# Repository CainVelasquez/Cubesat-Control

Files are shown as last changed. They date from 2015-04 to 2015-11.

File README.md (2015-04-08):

# Cubesat Controle

## Descrição
Desenvolvimento do sistema de controle de atitude

## Envolvidos
- Felipe
- Augusto
- William

## Organização das pastas

As pastas desse projeto devem ser organizadas conforme exemplo a seguir:

- Como : Toda documentação gerada e coletada que pode ser usada para compreenção e descrição do projeto

- Materiais : Todo formato de material desenvolvido no projeto, inclui softwares, esquemáticos, fotos, etc..

Árvore de arquivos :
```
└──  Materiais
├── Como
│   ├── Apresentações
│   ├── Artigos
│   │   └── Bibliografia
│   ├── Datasheets
│   ├── Estudos
│   ├── Manuais
│   └── Wiki
└──  Materiais
    ├── Arquivos
    │   └── Orçamentos
    ├── Códigos
    │   ├── Altera
    │   ├── Arduino
    │   ├── Atmel
    │   ├── C
    │   ├── Comsol
    │   ├── Labview
    │   ├── Matlab
    │   └── Xilinx
    ├── Fotos
    ├── Mecânica
    ├── PCB
    └── Referências
```

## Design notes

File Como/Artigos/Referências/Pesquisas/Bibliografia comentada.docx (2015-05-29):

| FLORENZANO, Teresa Gallotti. Iniciação em sensoriamento remoto. 3. ed. rev. e ampl. São Paulo, SP: Oficina de Textos, 2011. 128 p. ISBN 9788579750168.

- Utilizaremos para levantamento de histórico e informações básicas de funcionamento de satélites em geral;

| MISRA, Pratap; ENGE, Per. Global positioning system: signals, measurements, and performance. 2. ed. Massachusetts: Lincoln, 2011. 569 p. ISBN 9780970954428.

- Utilizaremos como base para posicionamento global, e informações básicas de funcionamento de satélite;

F.A.Martins_2014 - Projeto e desenvolvimento de um controlador de motores brushless para aplicação em volantes de inérica

- Utilizaremos como base este mestrado para o desenvolvimento do controle do motor BLDC. Aqui foi realizada uma placa com microcontrolador PIC, para acionamento do motor.

Brushless DC Motor Control Made Easy – AN857 Microchip

- Aqui temos um breve descritivo de como é o funcionamento de motores BLDC, e formas de controle, com sensores, ou sensorless. Open loop, closed-loop.

dsPICDEMTM MCLV DEVELOPMENT BOARD USER’S GUIDE

- Aqui é descrito o funcionamento da placa que utilizaremos para teste do motor BLDC, com exemplos de aplicação no ambiente MPLAB, e toda a parte eletrônica já realizada.

Sensored BLDC Motor Control Using dsPIC30F2010 AN957 Microchip

- Modelo de programa no MPLAB em linguagem C, para controle de motor BLDC;

Motor Maxon 351100

- Valores teóricos do motor, e especificações técnicas;

CONTROLE DE ATITUDE DE SATÉLITES ARTIFICIAIS – Trabalho de mestrado da ADRIELLE DE CARVALHO SANTANA

- Trabalho que será utilizado como guia para desenho do controle de atitude do Satelite

CubeSatBook – Princeton Satellite Systems, Inc.

- Guia de elaboração de um cubestat

CubeSat ELaNa III Launch on NPP Mission

- Exemplos de satelities lançados pela NASA

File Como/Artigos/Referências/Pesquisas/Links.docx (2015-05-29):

# Cubesat Attitude Control

https://www.youtube.com/watch?v=qoVHP34SqNg

# Reaction Wheel Pendulum

https://www.youtube.com/watch?v=UfKAn0wmxI0

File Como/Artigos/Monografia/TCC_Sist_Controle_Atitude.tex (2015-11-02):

%% abtex2-modelo-trabalho-academico.tex, v-1.9.1 laurocesar
%% Copyright 2012-2013 by abnTeX2 group at http://abntex2.googlecode.com/ 
%%
%% This work may be distributed and/or modified under the
%% conditions of the LaTeX Project Public License, either version 1.3
%% of this license or (at your option) any later version.
%% The latest version of this license is in
%%   http://www.latex-project.org/lppl.txt
%% and version 1.3 or later is part of all distributions of LaTeX
%% version 2005/12/01 or later.
%%
%% This work has the LPPL maintenance status `maintained'.
%% 
%% The Current Maintainer of this work is the abnTeX2 team, led
%% by Lauro César Araujo. Further information are available on 
%% http://abntex2.googlecode.com/
%%
%% This work consists of the files abntex2-modelo-trabalho-academico.tex,
%% abntex2-modelo-include-comandos and abntex2-modelo-references.bib
%%
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
	twoside,			% para impressão em páginas corretamente
	a4paper,			% tamanho do papel. 
	% -- opções da classe abntex2 --
	%chapter=TITLE,		% títulos de capítulos convertidos em letras maiúsculas
	%section=TITLE,		% títulos de seções convertidos em letras maiúsculas
	%subsection=TITLE,	% títulos de subseções convertidos em letras maiúsculas
	%subsubsection=TITLE,% títulos de subsubseções convertidos em letras maiúsculas
	% -- opções do pacote babel --
	english,			% idioma adicional para hifenização
	french,				% idioma adicional para hifenização
	spanish,			% idioma adicional para hifenização
	brazil,				% o último idioma é o principal do documento
	oldfontcommands
	]{abntex2}

% ---
% Pacotes básicos 
% ---
\usepackage{lmodern}			% Usa a fonte Latin Modern			
\usepackage[T1]{fontenc}		% Selecao de codigos de fonte.
\usepackage[utf8]{inputenc}		% Codificacao do documento (conversão automática dos acentos)
\usepackage{lastpage}			% Usado pela Ficha catalográfica
\usepackage{indentfirst}		% Indenta o primeiro parágrafo de cada seção.
\usepackage{color}				% Controle das cores
\usepackage{graphicx}			% Inclusão de gráficos
\usepackage{microtype} 			% Melhorias de justificação
\usepackage{pdfpages}			% Inserir páginas de pdf
\usepackage{amsmath}			% Funções Matemáticas
\usepackage{epstopdf}
% ---
		
% ---
% Pacotes adicionais, usados apenas no âmbito do Modelo Canônico do abnteX2
% ---
\usepackage{lipsum}				% para geração de dummy text
% ---

% ---
% Pacotes de citações
% ---
\usepackage[brazilian,hyperpageref]{backref}
% Paginas com as citações na bibl
\usepackage[num]{abntex2cite}	% Citações padrão ABNT

% --- 
% CONFIGURAÇÕES DE PACOTES
% --- 

% ---
% Configurações do pacote backref
% Usado sem a opção hyperpageref de backref
\renewcommand{\backrefpagesname}{Citado na(s) página(s):~}
% Texto padrão antes do número das páginas
\renewcommand{\backref}{}
% Define os textos da citação
\renewcommand*{\backrefalt}[4]{
	\ifcase #1 %
		Nenhuma citação no texto.%
	\or
		Citado na página #2.%
	\else
		Citado #1 vezes nas páginas #2.%
	\fi}%
% ---

% ---
% Informações de dados para CAPA e FOLHA DE ROSTO
% ---
\titulo{Sistema de controle de atitude para satélite CubeSat}
\autor{Augusto Bonangelo Costa\\
Felipe Ramos de Faria\\
William Mazi}
\local{São Caetano do Sul}
\data{2015}
\orientador{Prof. Dr. Rodrigo Alvite Romano}
%\coorientador{Professor}
\instituicao{Escola de Engenharia Mauá do Centro Universitário do Instituto Mauá de Tecnologia}
\tipotrabalho{Trabalho de Conclusão de Curso de Engenharia de Controle e Automação}
% O preambulo deve conter o tipo do trabalho, o objetivo, 
% o nome da instituição e a área de concentração 
\preambulo{Trabalho de Conclusão de Curso apresentado à Escola de Engenharia Mauá do Centro Universitário do Instituto Mauá de Tecnologia como requisito parcial para a obtenção do título de Engenheiro de Controle e Automação.}
% ---

% ---
% Configurações de aparência do PDF final

% alterando o aspecto da cor azul
\definecolor{blue}{RGB}{41,5,195}

% informações do PDF
\makeatletter
\hypersetup{
     	%pagebackref=true,
		pdftitle={\@title}, 
		pdfauthor={\@author},
    	pdfsubject={\imprimirpreambulo},
	    pdfcreator={LaTeX with abnTeX2},
		pdfkeywords={abnt}{latex}{abntex}{abntex2}{trabalho acadêmico}, 
		colorlinks=true,       		% false: boxed links; true: colored links
    	linkcolor=black,          	% color of internal links
    	citecolor=black,        	% color of links to bibliography
    	filecolor=black,      		% color of file links
		urlcolor=black,
		bookmarksdepth=4 
}
\makeatother
% --- 

% --- 
% Espaçamentos entre linhas e parágrafos 
% --- 

% O tamanho do parágrafo é dado por:
\setlength{\parindent}{1.25cm}

% Controle do espaçamento entre um parágrafo e outro:
\setlength{\parskip}{0.2cm}  % tente também \onelineskip

% ---
% compila o indice
% ---
\makeindex
% ---

% ----
% Início do documento
% ----
\begin{document}

% Retira espaço extra obsoleto entre as frases.
\frenchspacing

% ----------------------------------------------------------
% ELEMENTOS PRÉ-TEXTUAIS
% ----------------------------------------------------------
% \pretextual

% ---
% Capa
% ---
\imprimircapa
% ---

% ---
% Folha de rosto
% (o * indica que haverá a ficha bibliográfica)
% ---
\imprimirfolhaderosto*
% ---

% ---
% Inserir a ficha bibliografica
% ---

% Isto é um exemplo de Ficha Catalográfica, ou ``Dados internacionais de
% catalogação-na-publicação''. Você pode utilizar este modelo como referência. 
% Porém, provavelmente a biblioteca da sua universidade lhe fornecerá um PDF
% com a ficha catalográfica definitiva após a defesa do trabalho. Quando estiver
% com o documento, salve-o como PDF no diretório do seu projeto e substitua todo
% o conteúdo de implementação deste arquivo pelo comando abaixo:
%
% \begin{fichacatalografica}
%     \includepdf{fig_ficha_catalografica.pdf}
% \end{fichacatalografica}
\begin{fichacatalografica}
	\vspace*{\fill}					% Posição vertical
	\hrule							% Linha horizontal
	\begin{center}					% Minipage Centralizado
	\begin{minipage}[c]{12.5cm}		% Largura
	
	Costa, Augusto Bonangelo Costa
	
	\hspace{0.5cm} \imprimirtitulo  / Augusto Bonangelo Costa, Felipe Ramos de Faria, William Mazi. --
	\imprimirlocal, CEUN-IMT, \imprimirdata
	
	\hspace{0.5cm} \pageref{LastPage} p.\\
	
	\hspace{0.5cm}
	\parbox[t]{\textwidth}{\imprimirtipotrabalho~--~\imprimirinstituicao,
	\imprimirlocal, \imprimirdata.}\\
	
	\hspace{0.5cm} \imprimirorientadorRotulo~\imprimirorientador\\
	
	\hspace{0.5cm}
		1. Controle de Atitude.
		2. CubeSat.
		I. Faria, Felipe Ramos de
		II. Mazi, William
		III. Instituto Mauá de Tecnologia. Centro Universitário. Escola de Engenharia Mauá.
		IV. Título\\ 			
	
%	\hspace{8.75cm} CDU \\
	
	\end{minipage}
	\end{center}
	\hrule
\end{fichacatalografica}
% ---

% ---
% Inserir folha de aprovação
% ---

% Isto é um exemplo de Folha de aprovação, elemento obrigatório da NBR
% 14724/2011 (seção 4.2.1.3). Você pode utilizar este modelo até a aprovação
% do trabalho. Após isso, substitua todo o conteúdo deste arquivo por uma
% imagem da página assinada pela banca com o comando abaixo:
%
% \includepdf{folhadeaprovacao_final.pdf}
%
\begin{folhadeaprovacao}

  \begin{center}
    {\ABNTEXchapterfont\large\imprimirautor}

    \vspace*{\fill}\vspace*{\fill}
    \begin{center}
      \ABNTEXchapterfont\bfseries\Large\imprimirtitulo
    \end{center}
    \vspace*{\fill}
    
    \hspace{.45\textwidth}
    \begin{minipage}{.5\textwidth}
    \end{minipage}%
    \vspace*{\fill}
   \end{center}
        
Trabalho de Conclusão de Curso aprovado em \_\_\_ de \_\_\_\_\_\_\_\_\_\_\_\_\_ de 2015, pela banca examinadora composta por: 

   \assinatura{\textbf{\imprimirorientador} \\ Orientador} 
   \assinatura{\textbf{Professor} \\ Convidado 1}
   \assinatura{\textbf{Professor} \\ Convidado 2}
   %\assinatura{\textbf{Professor} \\ Convidado 3}
   %\assinatura{\textbf{Professor} \\ Convidado 4}
      
   \begin{center}
    \vspace*{0.5cm}
    {\large\imprimirlocal}
    \par
    {\large\imprimirdata}
    \vspace*{1cm}
  \end{center}
  
\end{folhadeaprovacao}
% ---

% ---
% Dedicatória
% ---

% ---
% Agradecimentos
% ---
\begin{agradecimentos}

A Escola de Engenharia Mauá por fornecer toda a gama de conhecimento e estrutura para um melhor aprendizado.\par

Ao {\imprimirorientador}  pela assessoria prestada quanto ao desenvolvimento do tema.\par

Ao Prof. Rafael Corsi por todo empenho dedicado auxiliando o projeto de distintas maneiras.\par

Ao técnico Fernando Nery Bueno por toda ajuda prestada durante diversas etapas do projeto.\par

E aos nossos pais, amigos e namoradas que apesar de todas as dificuldades sempre nos suportaram para o melhor desenvolvimento do projeto.

\end{agradecimentos}
% ---

% ---
% Epígrafe
% ---
\begin{epigrafe}
    \vspace*{\fill}
	\begin{flushright}
		\textit{Tudo aquilo que o homem ignora não existe para ele. Por isso o universo de cada um se resume ao tamanho de seu saber.\\(Albert Einstein)}
	\end{flushright}
\end{epigrafe}
% ---

% ---
% RESUMOS
% ---
% resumo em português
\setlength{\absparsep}{18pt} % ajusta o espaçamento dos parágrafos do resumo
\begin{resumo}
 Resumo do TCC

 \textbf{Palavras-chaves}: CubeSat, Controle de atitude, Satélite, Roda de reação, Sistemas embarcados.
\end{resumo}

% resumo em inglês
\begin{resumo}[Abstract]
 \begin{otherlanguage*}{english}
   This is the english abstract.

   \vspace{\onelineskip}
 
   \noindent 
   \textbf{Key-words}: CubeSat, Attitude control, Satellite, Reaction wheel, Embedded systems.
 \end{otherlanguage*}
\end{resumo}

% ---
% inserir lista de ilustrações
% ---
\pdfbookmark[0]{\listfigurename}{lof}
\listoffigures*
\cleardoublepage

% ---
% inserir lista de tabelas
% ---
\pdfbookmark[0]{\listtablename}{lot}
\listoftables*
\cleardoublepage

% ---
% inserir lista de abreviaturas e siglas
% ---
\begin{siglas}

  \item[AEB] {Agência Espacial Brasileira}
  \item[ADC] {Conversor Analógico-Digita}
  \item[BLDC] \textit{Brushless Direct Current Motor}
  \item[Cal Poly] \textit{California Polytechnic State University}
  \item[COTS] \textit{Commercial Off-The-Shelf}
  \item[CubeSat] \textit{Cube-Satellite}
  \item[DSP] \textit{Digital Signal Processing}
  \item[ESA] \textit{European Space Agency}
  \item[I$^{2}$C] \textit{Inter-Integrated Circuit}
  \item[IMT] {Instituto Mauá de Tecnologia}
  \item[IMU] \textit{Inercial Measurement Unit}
  \item[INPE] {Instituto Nacional de Pesquisas Espaciais}
  \item[ISS] \textit{International Space Station}
  \item[MIPS] {Milhões de Instruções Por Segundo}
  \item[NSA] \textit{National Aeronautics and Space Administration}
  \item[NSEE] {Núcleo de Sistemas Eletrônicos Embarcados}
  \item[U] \textit{Unit}
  \item[PI] {Proporcional-Integral}
  \item[PIC] \textit{Programmable Interface Controller}
  \item[PWM] \textit{Pulse-Width Modulation}
    
\end{siglas}

% ---
% inserir lista de símbolos
% ---
%\begin{simbolos}
%  \item[$ \Gamma $] Letra grega Gama
%  \item[$ \Lambda $] Lambda
%  \item[$ \zeta $] Letra grega minúscula zeta
%  \item[$ \in $] Pertence
%\end{simbolos}

% ---
% inserir o sumario
% ---
\pdfbookmark[0]{\contentsname}{toc}
\tableofcontents*
\cleardoublepage

% ----------------------------------------------------------
% ELEMENTOS TEXTUAIS
% ----------------------------------------------------------
\textual

% ----------------------------------------------------------
% Introdução (exemplo de capítulo sem numeração, mas presente no Sumário)
% ----------------------------------------------------------
\chapter{Introdução}

CubeSats (\textit{Cube-Satellite}) são satélites que possuem forma de cubo com aresta de 100mm e massa de até 1330g. Essas definições correspondem a uma unidade de CubeSat, que é representada pela sigla U (\textit{Unit}). É comum a utilização dessas unidades em conjuntos de 2U (200x100x100mm), 3U (300x100x100) ou 6U (300x200x100) \cite{NASA}. É utilizado como plataforma para realização de experimentos por instituições de ensino e pesquisa além de empresas que buscam uma solução de baixo custo para o desenvolvimento de novas tecnologias. O motivo pelo qual são necessárias pequenas quantias de investimentos é a utilização de materiais comerciais de prateleira (\textit{commercial off-the-shelf} - COTS), ou seja, materiais que podem ser encontrados no comércio, e de possuir um design padronizado que reduz tempo e custo de desenvolvimento \cite{CalPoly}.

Um dos principais sistemas dos satélites é o sistema de determinação e controle de atitude. A atitude é a orientação de um corpo em relação a uma referência externa em um dado sistema de coordenadas. O sistema de determinação e controle de atitude é composto por duas etapas principais: determinação de atitude e controle de atitude \cite{FrancLav}.

A determinação de atitude é o processo que envolve a aquisição de dados através de sensores de posicionamento que indicam para o sistema de controle de atitude qual a posição do satélite em relação a um referencial fixo \cite{FrancLav}. Esse processo possui elevada complexidade e, como não é objeto desse estudo, não será abordado com muita profundidade.

O controle de atitude é a atuação do sistema que movimentará o satélite, mudando sua posição em relação a um referencial. Em geral, o que define qual método de controle de atitude é empregado são a precisão do apontamento, a estabilidade, e a capacidade de manobra. Outros fatores também influenciam como custo, peso, confiabilidade, movimento orbital e vida útil. As várias formas de executar esse controle podem ser agrupadas em controle passivo ou controle ativo, de acordo com o tipo de torque \cite{FrancLav}.

O controle passivo pode ser feito de duas maneiras, por gradiente de gravidade, onde o eixo mais longo do satélite aponta para a Terra, mantendo assim uma orientação fixa em relação a mesma. Outro modo de controle passivo é através do alinhamento de um imã no satélite com as linhas de campo magnético da terra \cite{FrancLav}.

Já o controle ativo é feito de três formas principais. Uma delas consiste em manter o satélite girando em torno do eixo que aponta na direção desejada. Outro método é através de propulsores que geram impulso para a movimentação do satélite. Há ainda a manipulação de cada um dos ângulos de Euler (\textit{Roll-Pitch-Yaw}), o qual garante maior precisão no seu apontamento e facilita seu uso para experimentos científicos ou telecomunicações \cite{FrancLav}. Para este tipo de controle, os acionadores mais utilizados são as rodas de reação, os magnetorquers e os jatos de gás.

% ----------------------------------------------------------
% Justificativa
% ----------------------------------------------------------
\section{Justificativa}

	A área aeroespacial é importante para todo país que possui desenvolvimento tecnológico. A causa disso é a ajuda em desenvolver outras áreas paralelamente. Porém, desenvolvimentos de satélites são caros e o CubeSat entra como alternativa de baixo custo e acessível tanto a instituições de ensino quanto a empresas interessadas no setor \cite{DIY}.
	
Outro ponto positivo são as diversas aplicações que se dão a satélites, inclusive os do tipo CubeSat. Um exemplo é a pesquisa da "Anomalia do Atlântico Sul". Esta anomalia ocorre porque o campo magnético da Terra é mais fraco exatamente sobre a América do Sul e boa parte do Oceano Atlântico Sul, permitindo ondas magnéticas solares penetrarem mais fundo na atmosfera terrestre nesse ponto, causando interferência em satélites \cite{MORAES}. Um satélite do tipo CubeSat poderia ser usado para levantar mais dados a respeito desse fenômeno, através de medições diretas ou fotografias. Outro exemplo é utilizar o CubeSat para expor microrganismos ao ambiente espacial e analisar como se desenvolvem.

Além de todos estes motivos, um grande incentivo é nos iniciar na área espacial. Este estudo nos serve de base para aprender um pouco sobre soluções usando sistemas embarcados, sistemas de controle e diversas outras aplicações que nos podem ser úteis em nossas vidas profissionais, quaisquer que sejam nossas áreas de atuação.

% ----------------------------------------------------------
% Objetivo
% ----------------------------------------------------------
\section{Objetivos}

O objetivo deste estudo é projetar e construir o sistema de controle de atitude para um satélite do tipo CubeSat.

Este estudo servirá de base para o desenvolvimento de futuros CubeSats com melhores desempenhos e abrirá a possibilidade de que um deles possa ser enviado ao espaço com o objetivo de cumprir ou ajudar em alguma missão espacial.

\subsection{Objetivos primários}

Alguns dos principais objetivos deste trabalho são:

a)	modelagem e validação de sistemas;

b)	aprendizagem sobre rodas de reação;

c)	aprendizagem sobre softwares de projeto de placas de circuitos micro eletrônicos;

d)	aprendizagem sobre protocolo de comunicação I$^{2}$C;

e)	testes e validações do sistema de controle em um e mais graus de liberdade;

f) validação do motor \textit{brushless}.

% ----------------------------------------------------------
% Revisão bibliográfica
% ----------------------------------------------------------

\chapter{Revisão bibliográfica}

Como um guia para o trabalho, foi feito uma pesquisa bibliográfica sobre a qual o trabalho se baseou. Esta etapa da pesquisa tornou possível observar quem são os países que desenvolvem CubeSats, como é utilizado ao redor do mundo e como o Brasil está em relação aos desenvolvedores desta tecnologia, além de compreende as duas etapas que envolvem o módulo de atitude de um CubeSat, a determinação de atitude e o controle de atitude.

\section{Origem}

A concepção do CubeSat teve início no ano de 1999 através de um esforço em conjunto da Stanford University e California Polytechnic State University, que criaram as primeiras especificações que serviram de base para aos atuais CubeSats. O objetivo era possibilitar que estudantes pudessem projetar, construir, testar e operar um satélite com funcionalidades parecidas com as do Sputnik I, que eram emitir um sinal constante para a Terra, e medir a densidade da atmosfera \cite{SmallSat}.

\section{CubeSat no mundo} 

A maioria dos CubeSats lançados até hoje foram projetados, desenvolvidos e construídos nas universidades norte-americanas, como o XSAS, desenvolvido pela \textit{University of Michigan} \cite{MCKAY}, o \textit{Vermont Lunar CubeSat}, desenvolvido pela \textit{Vermont Technical College} \cite{Vermont}, além de outros desenvolvidos pelas veteranas \textit{Stanford University} \cite{TWIGGS} e \textit{California Polytechnic State University} \cite{PolySat}.

Algumas empresas privadas já desenvolveram seus próprios CubeSats, como é o caso da Boeing \cite{Boeing}. Eles desenvolveram um CubeSat com o objetivo de desenvolver sistemas de controle de atitude que seriam usados para refinar os sistemas usados nos aviões produzidos pela empresa.

Há ainda o caso da Planet Labs \cite{PlanetLabs}, empresa que desenvolveu e fabricou 28 CubeSats (de nome Dove) dotados de uma câmera fotográfica de alta resolução. Todos foram lançados ao espaço formando um conjunto chamado de Dove. Esse conjunto está espalhado pelo mundo. A Planet Labs vende o serviço fotográfico desses satélites. Sempre que alguém contrata esse serviço, eles tiram fotos do local especificado pela pessoa por um período. Esse serviço pode ser usado empresas de mineração, exploração de recursos naturais, monitoramento agrícola, monitoramento de desmatamento, etc. Isso mostra o quão abrangente são as possibilidades de uso dos CubeSats.

Diversos outros países já fizeram e lançaram ao menos um protótipo, como a Dinamarca, com o AAUSAT4, desenvolvido pela \textit{Aalborg University} \cite{AAUSAT}, o Canada, com o CANX-2, desenvolvido pela \textit{University of Toronto} \cite{CANX} e o Japão, com o CUTE 1, desenvolvido pela \textit{Tokyo Institute of Technology} \cite{CUTE}. Alguns países com pouco investimento em pesquisa espacial também possuem CubeSats, incluindo a Romênia, Hungria e Polônia \cite{ESA}, além de outros como a Lituânia e o Peru \cite{SpaceNews}. Isso os ajudou a serem inseridos no campo de pesquisa espacial.

\section{CubeSat no Brasil}

Destaca-se o projeto do CubeSat desenvolvido em uma parceria entre o Instituto Nacional de Pesquisas Espaciais (INPE) e o Instituto Tecnológico de Aeronáutica (ITA) \cite{AIT}, o qual foi projetado no Brasil. Ele foi lançado da ISS (\textit{International Space Station}, ou Estação Espacial Internacional) dia 5 de fevereiro de 2015 \cite{AEB}. Porém, uma antena de comunicação que deveria ser acionada trinta minutos após seu lançamento não foi acionada. Sendo assim, foi considerado inoperante \cite{ITA}.

\section{Determinação de atitude}

Para que o controle de atitude seja eficiente, é necessário ter uma determinação de atitude confiável. Para tal, precisa-se de um conjunto de sensores com precisão compatível. Os sensores mais comuns utilizados para essa finalidade são o sensor solar, magnetômetro, giroscópio e sensor estrelar \cite{FrancLav}.

Os sensores solares são os mais comumente utilizados. Eles medem o ângulo de incidência dos raios solares e utilizam esses dados para referenciar um ou dois ângulos. Eles fornecem uma precisão que chega a ser menor do que um grau, mas não são operacionais durante eclipses \cite{FrancLav}.

Os magnetômetros são sensores simples e leves que medem o campo magnético do ambiente. Um magnetômetro de três eixos pode medir até dois graus válidos para o controle de atitude. Sua precisão é por volta de um grau, isso devido à inconstância do campo magnético da Terra. Porém, eles não podem ser usados em conjunto com magnetorquers, uma vez que o magnetômetro seria influenciado pelo campo magnético do magnetorquer \cite{FrancLav}.

Giroscópios são o tipo de sensor mais barato, mas não fornecem a direção dos eixos diretamente como fazem os outros sensores. Eles detectam a rotação em torno de cada um dos eixos e necessita ser usado em conjunto com outro sensor, uma vez que a direção dos eixos é desconhecida \cite{FrancLav}.

O sensor estrelar é um dispositivo óptico que mede o posicionamento das estrelas utilizando fotocélulas. Ele compara as medições com um banco de dados para determinar a atitude e seu posicionamento no espaço. Este sensor possui a precisão de $0,1^{\circ}$, sendo assim um dos mais precisos que existe, porém possui o inconveniente de ser muito maior e mais pesado em comparação aos outros, além de possuir um custo extremamente elevado, requerer um processamento muito alto e uma banda de resposta reduzida \cite{FrancLav}.

\section{Controle de atitude}

O controle de atitude é feito através de atuadores que variam e muito de aplicação em aplicação. O controle é dividido em duas categorias, controle passivo e controle ativo. O controle passivo é todo aquele em que o posicionamento do satélite é feito através da tendência do mesmo em ficar em uma determinada posição. Isso significa que o satélite não pode mudar seu posicionamento, isso é definido na fase de projeto e não pode ser alterado. É usado apenas quando não há necessidade de controlar o posicionamento dele. Pode ser feito por gradiente de gravidade ou alinhamento das linhas de campo magnético. Já controle ativo é quando o posicionamento do satélite importa e precisa ser alterado. Pode ser feito através da estabilização por rotação, propulsão ou estabilização dos três eixos \cite{FrancLav}.

Para usar o método de estabilização por gradiente de inércia, o CubeSat deve ser do tipo 2U ou superior, uma vez que é necessário possuir um eixo muito mais longo que os outros. Esse eixo, que possui menor momento de inércia, ficará apontado para o centro da Terra. É um método que permite o satélite a sempre voltar para a mesma posição, mas o tempo em que isso ocorre pode variar, além dele tender a ficar oscilando em torno do eixo vertical \cite{FrancLav}.

O método de alinhamento por campo magnético é um pouco mais sofisticado, nele são colocadas bobinas, hastes magnéticas ou ímãs permanentes no satélite que geram um campo magnético próprio que tende a se orientar com o da Terra, como ilustrado na Figura \ref{fig:Mag_Field}. Pode ser utilizado sem restrições de tamanho, mas é pouco preciso, uma vez que o campo magnético da Terra é extremamente variável \cite{FrancLav}. Uma variação comum é a utilização de magnetorquers, que são basicamente hastes magnéticas que geram um campo magnético que interage com o da Terra, formando um torque e movendo o satélite. Essa já é uma forma de controle ativo mas pode interferir na medição de alguns tipos de sensores.

\begin{figure}[th]
	\caption{Alinhamento por campo magnético.}
	\centering
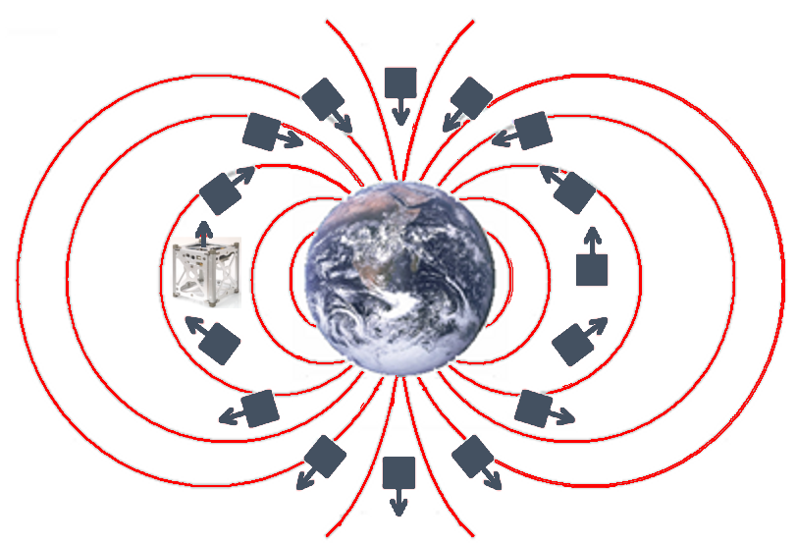
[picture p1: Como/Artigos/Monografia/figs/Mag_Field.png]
	
	
	\begin{small}
		FONTE: \cite{FrancLav}
	\end{small}
	\label{fig:Mag_Field}
\end{figure}

\newpage

O método da estabilização por rotação é uma melhoria do método passivo por alinhamento. Nele, o satélite permanece apontado para uma posição fixa e rotaciona ao redor do eixo principal. Apesar do controle não permitir mudanças bruscas no apontamento do eixo principal, que assim como o método passivo, deve ser definido durante a fase de projeto, essa rotação cria uma inércia que o torna robusto a perturbações, aumentando a precisão do apontamento \cite{FrancLav}.

O método da propulsão é muito pouco utilizado em CubeSats. Consiste em jatos de gás ou foguetes monopropulsores, que trabalham normalmente em pares, posicionados ao redor do satélite de forma que gerem um impulso inicial, provocando um torque. A vantagem dessa forma de controle é que pode ser usada também para translação do CubeSat, como ilustrado na Figura \ref{fig:Propulsion} a seguir. Porém, como ocupa muito espaço, tanto para o próprio propulsor quanto para o combustível que utiliza, é utilizado apenas em CubeSats com pelo menos 3U \cite{Luka}.

\begin{figure}[th]
	\caption{Controle através de propulsão.}
	\centering
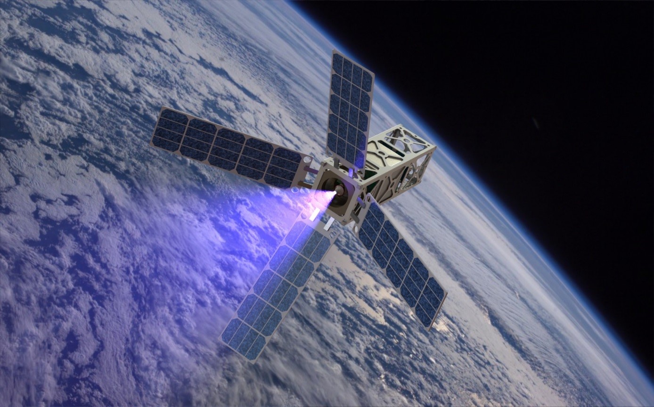
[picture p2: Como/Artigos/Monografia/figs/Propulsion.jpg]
	
	
	\begin{small}
		FONTE: \cite{Prop}
	\end{small}
	\label{fig:Propulsion}
\end{figure}

%\newpage

O método da estabilização dos três eixos é o método mais comumente utilizado, já que é versátil e usa pouco espaço, além de ser o mais eficiente. Ele se baseia na terceira Lei de Newton, que diz: \textit{''Para toda ação, há sempre uma reação oposta e de igual intensidade''}. Isso significa que se há uma massa acelerando presa ao satélite, ela irá forçar o mesmo a girar na direção oposta. Quanto maior o valor dessa massa, mais influência ela terá sobre o sistema \cite{Ericksson}. As rodas de reação fazem o papel dessa massa ao serem fixadas ao eixo de motores (normalmente \textit{brushless}) e dispostos cada um em um eixo, possibilitando realizar manobras de rolagem (\textit{roll} ou X), arfagem (\textit{pitch} ou Y) e guinada (\textit{yaw} ou Z). Um exemplo desse conjunto de motor e roda de reação é mostrado a seguir, na Figura \ref{fig:SRW}.

\begin{figure}[th]
	\caption{Conjunto motor e roda de reação.}
	\centering
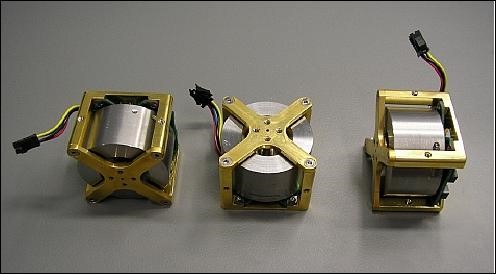
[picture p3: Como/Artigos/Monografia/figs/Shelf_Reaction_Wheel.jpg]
	
	
	\begin{small}
		FONTE: \cite{SWR}
	\end{small}
	\label{fig:SRW}
\end{figure}

%\newpage 

Há ainda dois tipos de controle através desse método, um com quatro e outro com três conjuntos motor-roda de reação. O modelo que utiliza quatro conjuntos possui controle mais complexo, uma vez que estes conjuntos são dispostos de forma que o somatório das rotações forma o torque desejado, como mostra a Figura \ref{fig:ERW} a seguir. Este método é amplamente utilizado pois caso um dos motores pare de funcionar, os outros três podem compensa-lo, aumentando a vida útil do satélite \cite{Ericksson}.

\begin{figure}[th]
	\caption{Modelo com quatro conjuntos motor-roda de reação e duas hastes magnéticas.}
	\centering
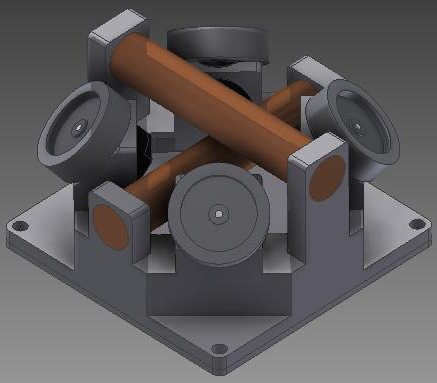
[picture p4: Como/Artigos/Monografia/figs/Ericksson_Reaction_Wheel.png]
	
	
	\begin{small}
		FONTE: \cite{Ericksson}
	\end{small}
	\label{fig:ERW}
\end{figure}

\newpage

Já o modelo de três conjuntos motor-roda de reação é mais simples, cada conjunto atua diretamente em um eixo, controlando-o diretamente, como mostrado a seguir pela Figura \ref{fig:3RW}. Sua maior desvantagem é que caso um dos motores pare de funcionar, o movimento do satélite no eixo correspondente também cessa. Esse é o método adotado e explorado nesse trabalho.

\begin{figure}[th]
	\caption{Modelo com três conjuntos motor-roda de reação.}
	\centering
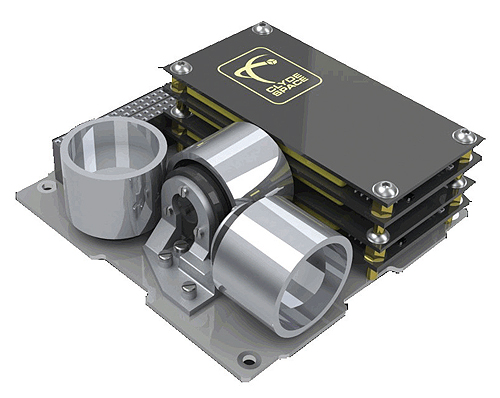
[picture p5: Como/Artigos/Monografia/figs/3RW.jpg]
	
	
	\begin{small}
		FONTE: \cite{3RW}
	\end{small}
	\label{fig:3RW}
\end{figure}

%\newpage

% ----------------------------------------------------------
% Materiais e Métodos
% ----------------------------------------------------------
%\chapter[Materiais e Métodos]{Materiais e métodos}

%Para facilitar a compreensão das partes que envolvem o projeto, os itens foram divididos em duas categorias:
%Materiais, focada em explicar quais os materiais utilizados para a construção do CubeSat e porquê.
%Métodos, focada em explicar como foi feita a integração dos materiais, programações necessárias, cálculos de equações de modelagem e controle, etc.

% ----------------------------------------------------------
% Materiais
% ----------------------------------------------------------
\chapter{Materiais}

Os materiais utilizados para a construção de CubeSats são COTS, isso significa que a maior parte deles foi comprada e implementada diretamente, sem necessidade de adaptações.

\section{Sensor}

Como a determinação de atitude não é objeto de estudo deste trabalho, não será abordado um método para escolha do melhor sensor. Adotamos uma \textit{Inertial Measurement Unit} (IMU) HMC6343 (Honeywell, EUA), mostrado a seguir na Figura \ref{fig:IMU}, que é a combinação de três magnetômetros e três acelerômetros, cada um disposto em um eixo, de forma a compor as informações de rotação dos três eixos. Sua precisão é de cerca de $1^{\circ}$ em para \textit{Roll} e \textit{Pitch} e $2^{\circ}$ para \textit{Yaw}, uma precisão ótima para a nossa aplicação, além de ter um tamanho extremamente compacto (9x9mm). Essa IMU fornece os dados já tratados através de uma porta de comunicação I$^{2}$C.

\begin{figure}[th]
	\caption{IMU utilizada.}
	\centering
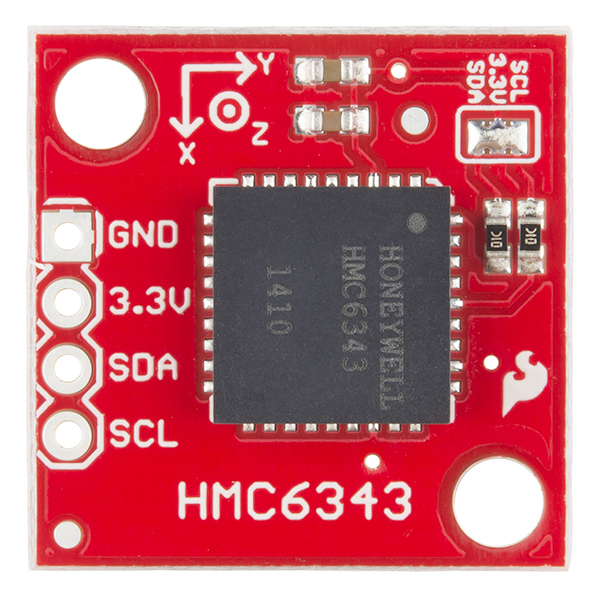
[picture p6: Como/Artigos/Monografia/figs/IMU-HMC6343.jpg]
	
	
	\begin{small}
		FONTE: \cite{IMU}
	\end{small}
	\label{fig:IMU}
\end{figure}

%\newpage

\section{Circuitos e componentes eletrônicos}

O objetivo do conjunto de circuitos eletrônicos é possibilitar o controle de velocidade independente dos três motores, cada um com um microcontrolador, um driver e um sensor de corrente. Para comandar o conjunto é necessário um microcontrolador principal, responsável por enviar \textit{set points} de velocidades de acordo com a leitura do sensor de posicionamento conforme definido pela sua malha de controle. A comunicação entre esses quatro dispositivos é realizada por duas redes I$^{2}$C: uma para leitura do sensor e uma para comunicação entre microcontroladores.

As soluções de hardware que satisfazem os requisitos de desempenho para um Cubesat são abundantes no mercado internacional \cite{STATEOFART}. Desta forma os critérios de escolha muitas vezes são o custo, o risco e a disponibilidade dos itens no fabricante.

\subsection{Microcontrolador}

A capacidade de processamento que um satélite precisa já está disponível no mercado. A velocidade recomendada de um processador para um CubeSat é de aproximadamente 30 MIPS. Além do tamanho dos componentes, sempre é necessário um cuidado especial com o consumo de energia \cite{STATEOFART}.

Os microprocessadores selecionados foram da família dsPIC33EP. Eles possuem capacidade de processamento de 60 MIPS operando de $-40^{\circ}$C até $+125^{\circ}$C. Possuem modo de gerenciamento de baixo consumo de energia, módulo DSP, que consiste em um multiplicador de alta velocidade capaz de realizar multiplicações com 17 bits e somas ou subtrações com 40 bits. Seu diferencial para controle de motores BLDC aparece em seus três módulos independentes de PWM de alta velocidade, que podem gerar disparos ao modulo ADC. Outra ferramenta que será utilizada no controle do motor é o \textit{Input Capture}, que é utilizado em aplicações que requerem medidas de períodos e frequências \cite{dsPIC33EP}. Todas essas ferramentas serão compiladas no ambiente MPLAB X IDE utilizando o compilador XC16, ambos do fabricante Microchip.

O microcontrolador utilizado na placa de controle é o dsPIC33EP32MC502 (Microchip, EUA) onde o seu circuito é apresentado na Figura \ref{fig:dsPIC502} a seguir. 

\begin{figure}[th]
	\caption{Microcontrolador dsPIC33EP32MC502.}
	\centering
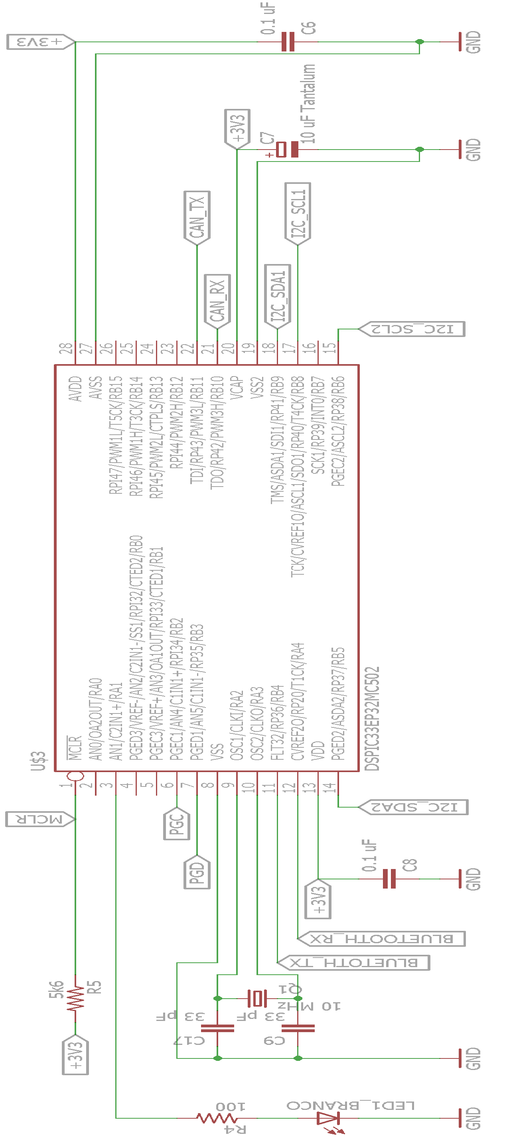
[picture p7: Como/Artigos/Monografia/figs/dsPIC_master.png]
	
	
	\begin{small}
		FONTE: Arquivo dos autores.
	\end{small}
	\label{fig:dsPIC502}
\end{figure} 

\newpage

O microcontrolador utilizado na placa de acionamento do motor é o dsPIC33EP32MC202 (Microchip, EUA) onde o seu circuito é apresentado na Figura \ref{fig:dsPIC202} a seguir.

\begin{figure}[th]
	\caption{Microcontrolador dsPIC33EP32MC202.}
	\centering
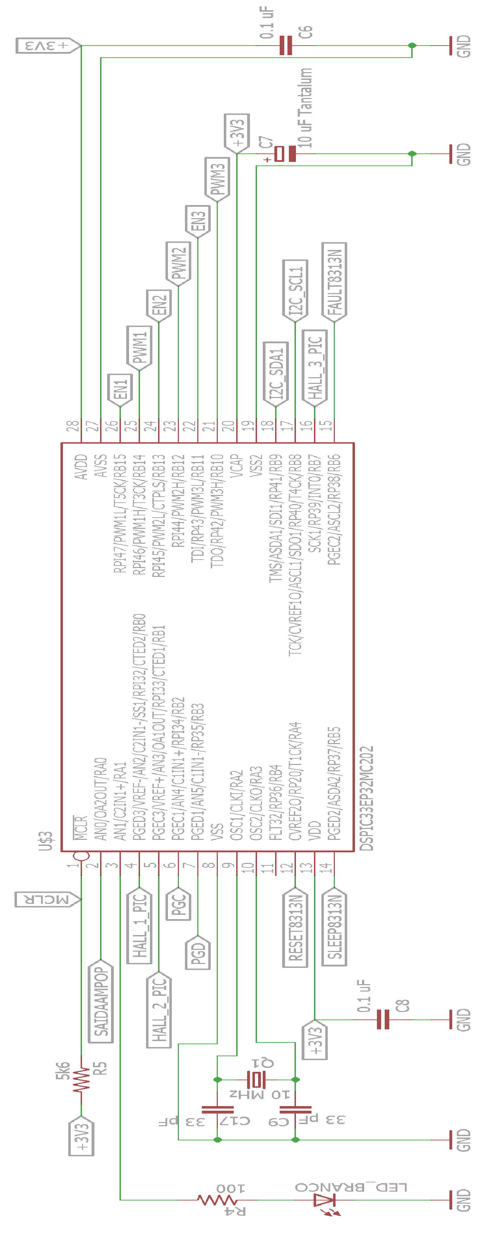
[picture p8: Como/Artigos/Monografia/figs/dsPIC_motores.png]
	
	
	\begin{small}
		FONTE: Arquivo dos autores.
	\end{small}
	\label{fig:dsPIC202}
\end{figure} 

\newpage

\subsection{\textit{Driver} de acionamento do motor}

Para o acionamento do motor foi selecionado o circuito integrado DRV8313 (Texas Instruments, EUA). O DRV8313 possui três meias pontes H que suportam $2.5A$ de corrente de pico e podem alimentar o motor com tensões de $8$ a $60V$ além de possuir circuitos de proteção contra sobre-corrente, curto circuito e subtenção.\cite{DRV8313}. O driver destina-se a aplicações de acionamento de motores BLDC de três fases, mas pode ser utilizado também para acionamento de solenoides. Possui a funcionalidade de \textit{sleep mode}, que pode ser ativada quando não é preciso fazer controle de velocidade do motor e auxilia no consumo de energia e por fim pode reportar falhas em sua operação através do pino \textit{FAULT}, conforme a Figura \ref{fig:Driver} a seguir.

\begin{figure}[th]
	\caption{Driver DRV8313.}
	\centering
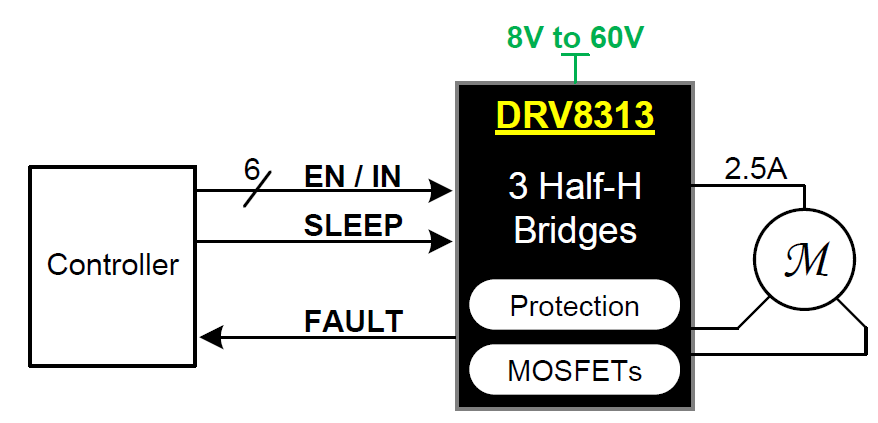
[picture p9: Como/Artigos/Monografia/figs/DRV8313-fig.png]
	
	
	\begin{small}
		FONTE: \cite{DRV8313}
	\end{small}
	\label{fig:Driver}
\end{figure}

%\newpage

\subsection{Interfaces e barramentos}

Enquanto os famosos \textit{Universal Serial Bus} (USB) e o \textit{Controller Area Network} (CAN) são protocolos de comunicação usados esporadicamente, o protocolo I$^{2}$C aparece como o barramento mais utilizado para nano satélites, devido ao seu baixo consumo de energia, além de estar disponível na maioria dos microcontroladores. Outros tipos de interfaces para diferentes tipos de fluxo de dados são desejáveis. \cite{STATEOFART}

O barramento de comunicação da placa de controle é composto por duas redes I$^{2}$C, uma para a comunicação com a IMU e outra para a comunicação com os outros microcontroladores. Também estão disponíveis no conjunto uma interface CAN e uma USART – \textit{Universal Synchronous/Asynchronous Receiver/Transmitter} além de interface ICSP – \textit{In-Circuit Serial Programming} para a programação do microcontrolador.

%\begin{figure}[th]
%	\caption{Barramento de comunicação.}
%	\centering
%	\includegraphics[width=0.8\linewidth]{./figs/Barra_pino_master}
	
%	\begin{small}
%		FONTE: Arquivo dos autores.
%	\end{small}
%	\label{fig:Barra_pino_master}
%\end{figure}

A placa de controle é responsável também por receber a alimentação 12V da bateria e distribuir para as outras placas através de seu barramento de alimentação.

%\begin{figure}[th]
%	\caption{Barramento de alimentação.}
%	\centering
%	\includegraphics[width=0.8\linewidth]{./figs/Barra_pino_alimentacao_master}
	
%	\begin{small}
%		FONTE: Arquivo dos autores.
%	\end{small}
%	\label{fig:Barra_pino_alimentacao_master}
%\end{figure} 

No barramento de comunicação da placa de acionamento do motor, existe interface para comunicação I$^{2}$C, alimentação e interface ICSP – \textit{In-Circuit Serial Programming} para programação do microcontrolador.

%\begin{figure}[th]
%	\caption{Barramento da placa de motor.}
%	\centering
%	\includegraphics[width=0.8\linewidth]{./figs/Barra_pino_motores}
	
%	\begin{small}
%		FONTE: Arquivo dos autores.
%	\end{small}
%	\label{fig:Barra_pino_motores}
%\end{figure} 

\subsection{Medidor de corrente}

Para o sistema de controle do BLDC é necessário conhecer a corrente que está passando pelo motor. A aquisição é feita através da medição de tensão sobre um resistor \textit{shunt} de $0,5\Omega$ colocado  em série com o motor. 

O valor dessa tensão é muito pequeno, variando de 0 até 243mV quando o motor estiver com 100\% de PWM, sendo assim necessária a amplificação desse sinal. Para isso foi utilizado um amplificador operacional LMV358 (Texas Instruments, EUA) configurado conforme a Figura \ref{fig:Medidor_corrente}.

\begin{figure}[th]
	\caption{Medidor de corrente.}
	\centering
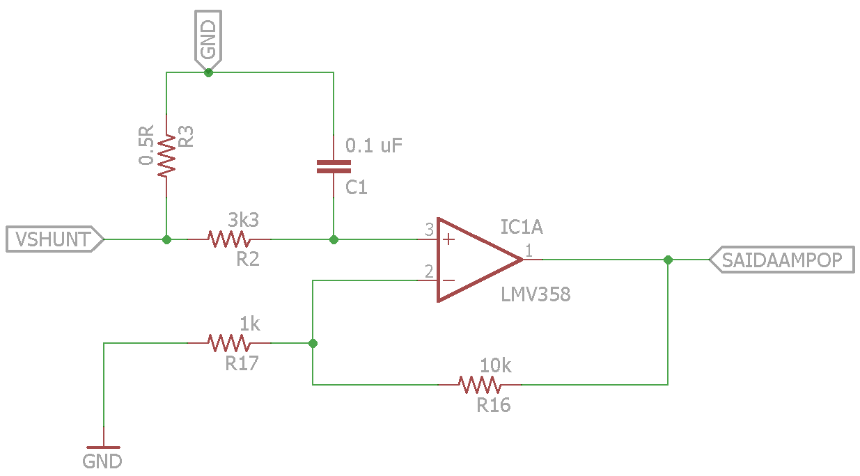
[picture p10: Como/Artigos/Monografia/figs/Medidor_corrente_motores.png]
	
	
	\begin{small}
		FONTE: Arquivo dos autores.
	\end{small}
	\label{fig:Medidor_corrente}
\end{figure}

%\newpage

Como pode ser observado na imagem, existe um filtro com frequência de corte de 482Hz com o objetivo de filtrar pequenos ruídos e a forma de onda do PWM, pois estes também serão amplificados se não filtrados, prejudicando a medição da tensão.

O amplificador está configurado para que sua saída que é não inversora ter uma ganho de 11 vezes em relação a sua entrada, ou seja, a sua saída terá o valor máximo de aproximadamente 2,7V.

A saída do amplificador operacional é conectada em uma entrada do microcontrolador que possua o módulo de conversão analógica para que seja feita a conversão do sinal para valor digital.  

\subsection{Divisor de tensão com resistências}

Os sensores de efeito Hall do motor possuem alimentação de 12V porém o microcontrolador é tolerante com tensões de até 5V. Nesse caso é necessário a construção de um divisor de tensão com resistências  conforme a Figura \ref{fig:Divisor_tensao}. 

\begin{figure}[th]
	\caption{Divisor de tensão com resistências.}
	\centering
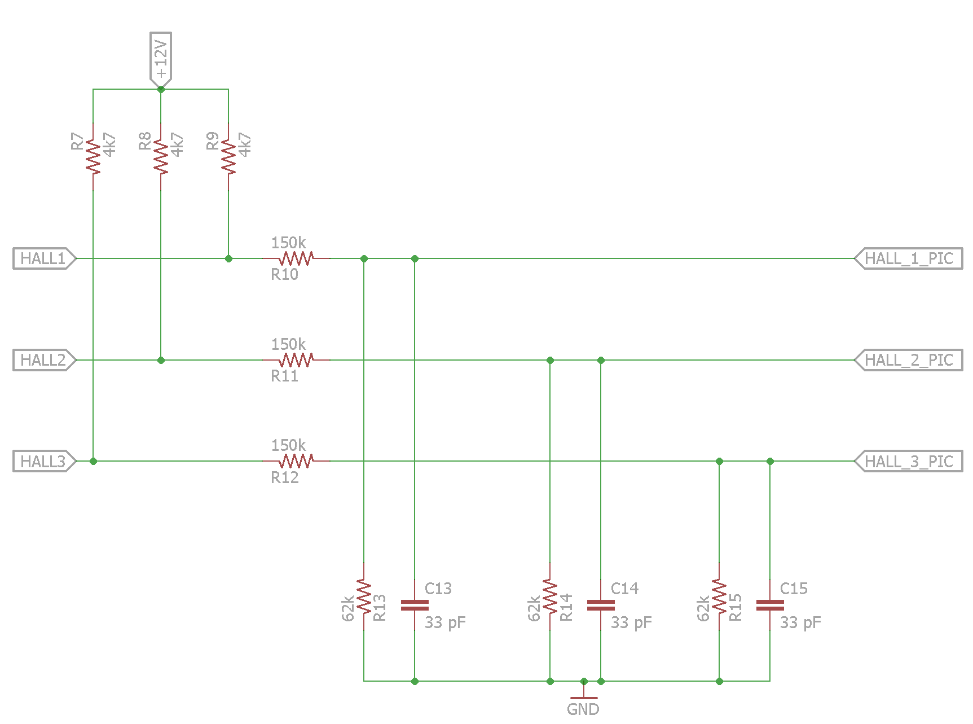
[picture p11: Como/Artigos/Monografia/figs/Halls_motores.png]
	
	
	\begin{small}
		FONTE: Arquivo dos autores.
	\end{small}
	\label{fig:Divisor_tensao}
\end{figure}

\newpage

Os resistores foram dimensionados de forma que a tensão de saída seja igual a 3,51V. Foi elaborado também um filtro com frequência de corte de 32153Hz para filtrar pequenos ruídos e também \textit{pull-up} em cada sensor Hall do motor.

\subsection{Regulador de tensão}

As placas eletrônicas são alimentadas com 12V porém, toda a parte lógica do circuito deve ser alimentada 3,3V. Nesta situação, é utilizado o regulador de tensão REG1117-3.3 (Texas Instruments, EUA) que retifica a tensão de 12V para 3,3V e possui a capacidade de fornecer até 800mA, o suficiente para alimentar todos os componentes.

\subsection{Placas de circuito eletrônico}

Devido ao espaço reduzido dentro do CubeSat, é necessário dividir funções para cada placa eletrônica, ou seja, o CubeSat possui uma placa de controle e três placas responsáveis cada uma por acionar um motor.

\subsubsection{Placa de controle}

A placa de controle é responsável por receber os dados da IMU, processar esse dados, gerar o \textit{set point} de cada motor e enviar esse \textit{set point} para sua respectiva placa de acionamento. Essa placa possui os seguintes componentes e circuitos: microcontrolador, regulador de tensão, barramento de comunicação e barramento de alimentação. A placa de circuito eletrônico pode ser vista no Apêndice \ref{ap:PMaster}. 

\subsubsection{Placa de acionamento dos motores}

A placa de acionamento dos motores é responsável por receber o \textit{set point} da placa de controle, fazer o controle da ordem de acionamento das bobinas do motor através dos sensores de efeito Hall, medir a corrente que está passando pelo motor, processar a lei de controle e acionar o motor. A placa de acionamento possui um regulador de tensão, um divisor de tensão, um circuito medidor de corrente, barramento de comunicação e barramento de alimentação.  A placa de circuito eletrônico pode ser vista no Apêndice \ref{ap:PMotor}.

\subsubsection{Lista de componentes}

A seguir, na Tabela \ref{tab:CompElet}, a lista de componentes usados na confecção de ambas as placas. Nos locais onde há um asterisco indicado, o componente é compartilhado entre ambas as placas.

\begin{table}[h]
	\caption{Lista de componentes eletrônicos.}
		\centering
	\begin{tabular}{|c|c|c|}
		\hline
		\textbf{Descrição} & \textbf{Quantidade} & \textbf{Quantidade}\\
		  & \textbf{placa motor} & \textbf{placa controle} \\
		\hline 
		Regulador de tensão REG1117 & 1 & 1 \\ 
		\hline 
		Conector  1-84953-1 & 1 & \\ 
		\hline 
		Resistor shunt $0,5\Omega$, 1W, 1\% & 1 & \\
		\hline 
		Amplificador operacional LMV358 & 1 & \\
		\hline 
		Circuito integrado DRV8313 & 1 & \\
		\hline 
		Microcontrolador dsPIC33EP32MC502 & 1 & 1 \\
		\hline 
		Capacitor eletrolítico $47\mu$F & 4 & 4 \\
		\hline
		Capacitor eletrolítico $10\mu$F & 1 & \\
		\hline
		Capacitor cerêmico $0,1\mu$F & 7 & 2 \\
		\hline
		Capacitor cerêmico 33pF & 5 & 2 \\
		\hline
		Capacitor de tântalo $10\mu$F & 1 & 1 \\
		\hline
		Resistor $100\Omega$ & 2 & 1 \\
		\hline
		Resistor $1k\Omega$ & 1 & \\
		\hline
		Resistor $3k3\Omega$ & 1 & \\
		\hline
		Resistor $4k7\Omega$ & 3 & \\
		\hline
		Resistor $5k6\Omega$ & 1 & 1 \\
		\hline
		Resistor $10k\Omega$ & 1 & 4 \\
		\hline
		Resistor $62k\Omega$ & 3 & \\
		\hline
		Resistor $150k\Omega$ & 3 & \\
		\hline
		Led branco & 1 & 1 \\
		\hline
		Led verde & 1 & \\
		\hline
		Cristal 10MHz & 1 & 1 \\
		\hline
		Barra de pino 20x2 & 1 & 3 \\
		\hline
		Bateria 1300mAh & 1 & * \\
		\hline
		Conector XT60 fêmea & 1 & * \\
		\hline
		Módulo bluetooth HM-10 & 1 & * \\
		\hline
		Cabinho jumper & 60 & * \\
		\hline
	\end{tabular}
	
	\begin{small}
	\vspace{3pt}	
	FONTE: Dos autores.
	\end{small}
	\label{tab:CompElet}
\end{table}

\newpage

\section{Atuador}

Para integração do motor adotado com a roda de ação, foi criado um conjunto padrão que consiste em um suporte para o motor, o motor e a roda de reação. Foi utilizado um desses conjuntos em cada um dos eixos correspondentes ao \textit{roll}, \textit{pitch} e \textit{yaw} como mostrado na Figura \ref{fig:MotSet} a seguir.

\begin{figure}[th]
	\caption{Conjunto para acoplamento do motor ao CubeSat.}
	\centering
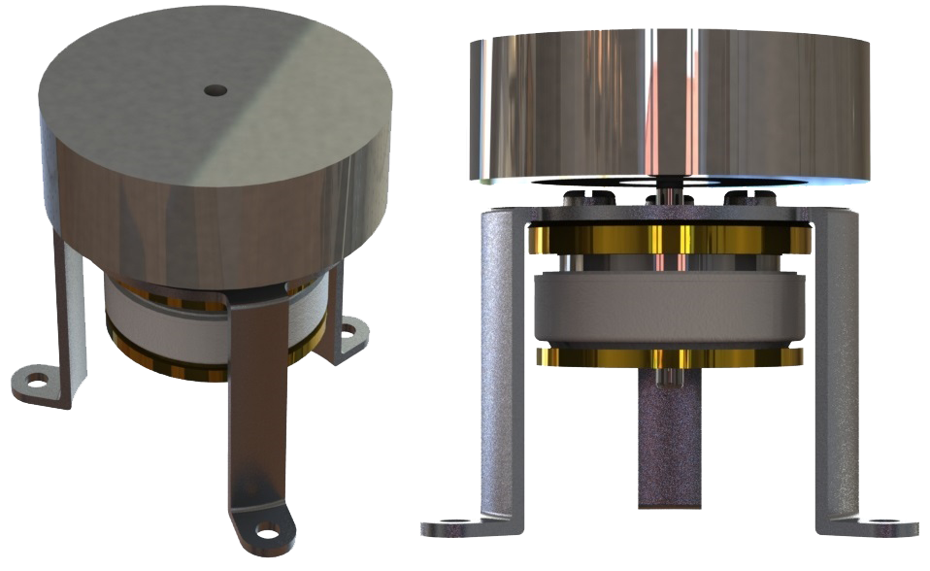
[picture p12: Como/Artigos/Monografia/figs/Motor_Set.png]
	
	
	\begin{small}
		FONTE: Arquivo dos autores.
	\end{small}
	\label{fig:MotSet}
\end{figure}

\newpage

\subsection{Motor}

Para escolha do motor, foi levado em consideração principalmente dois fatores: tipo e tamanho \cite{Ericksson}.

Costumeiramente, CubeSats utilizam motores de corrente contínua sem escovas (\textit{brushless direct current motor} – BLDC). A NASA recomenda o uso de motores desse tipo para aplicações aeroespaciais \cite{NASABLDC}. A Tabela \ref{tab:VnteDesv} a seguir mostra um comparativo das principais vantagens do uso de um motor \textit{brushless} na área aeroespacial segundo a NASA.

\begin{table}[h]
	\caption{Vantagens e desvantagens de um motor \textit{Brushless}.}
		\centering
	\begin{tabular}{|c|c|}
		\hline
		\textbf{Vantagens} & \textbf{Desvantagens} \\ 
		\hline 
		Alta velocidade (até 100000RPM) & Circuitos mais caros \\ 
		\hline 
		Alto torque a altas velocidades & Maior complexidade do driver do motor \\ 
		\hline 
		Aproximadamente o dobro de torque & \\
		 de saída quando comparado a motores & \\
		  com escova do mesmo tamanho &  \\ 
		\hline 
		Enrolamentos no estator ao invés & \\
		 do rotor melhoram a dissipação & \\
		  de calor & \\ 
		\hline 
		Sem escovas, então os motores & \\
		 duram enquanto durarem os & \\
		  rolamentos & \\ 
		\hline 
		Alta eficiência & \\ 
		\hline 
		Bom desempenho no vácuo & \\ 
		\hline
	\end{tabular}
	
	\begin{small}
	\vspace{3pt}	
	FONTE: \cite{Ericksson}
	\end{small}
	\label{tab:VnteDesv}
\end{table}

%\newpage

O tamanho do motor também é um fator limitante pois o espaço dentro de um CubeSat é extremamente limitado. Quanto menor o tamanho dos motores, mais fácil de acomodá-los e mais espaço sobra para utilizar com outros fatores, como a bateria no caso de um CubeSat de 1U ou para acomodar outras pesquisas que o CubeSat possa estar levando \cite{Martins}. A seguir, na Figura \ref{fig:Maxon}, um exemplo de motor BLDC normalmente utilizado em CubeSats.

\begin{figure}[th]
	\caption{Motor Maxon 351100, a moeda serve para referência quanto às dimensões.}
	\centering
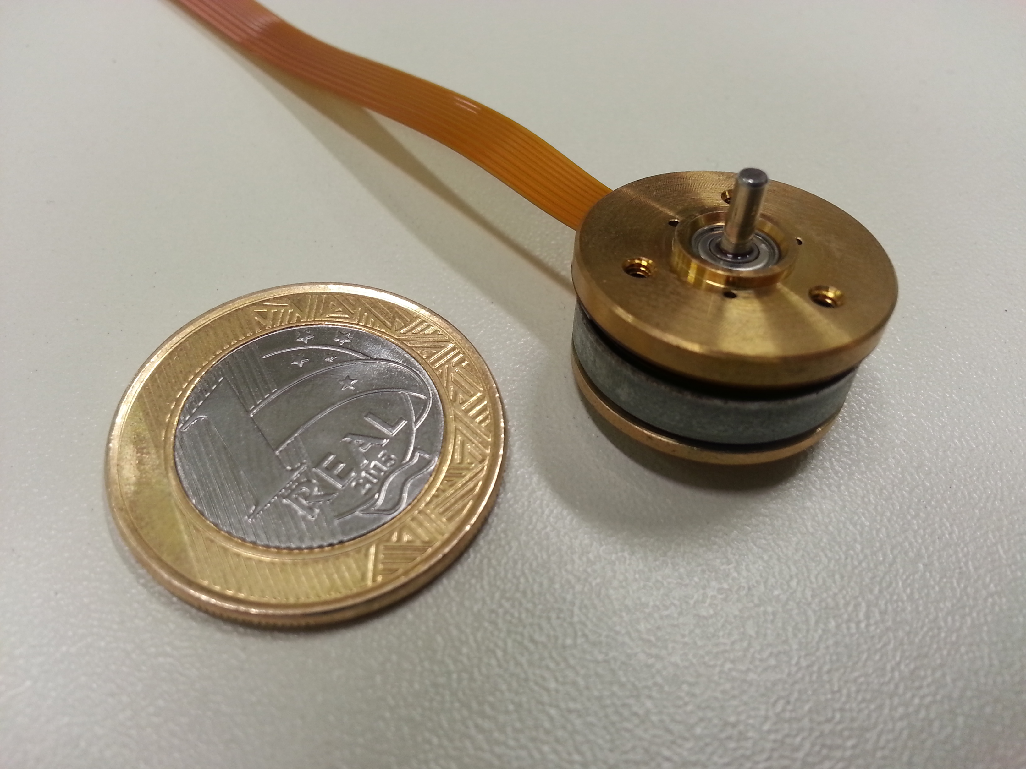
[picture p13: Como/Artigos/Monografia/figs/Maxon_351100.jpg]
	
	
	\begin{small}
		FONTE: Arquivo dos autores.
	\end{small}
	\label{fig:Maxon}
\end{figure}

%\newpage

O motor que melhor atende a todos estes requisitos e portanto o utilizado neste trabalho é o motor \textit{brushless} modelo 351100 (Maxon, Suíça). O catálogo com as especificações técnicas deste motor encontram-se no Anexo \ref{an:MM}.

%O motor já estava definido e disponível no início do projeto pelo NSEE (Núcleo de Sistemas Eletrônicos Embarcados) como um dos objetivos do estudo, validando o uso de um motor \textit{brushless} de 3W.

\subsection{Rodas de reação}

A roda de reação é basicamente um disco rotativo com muita massa (em relação ao resto do sistema). Quanto maior a massa e a geometria dela, maior a inércia I(kgm$^{2}$), como demonstrado na Equação \ref{eq:Inercia}, onde m(kg) é a massa e r(m) é o raio da roda. A inércia cresce proporcionalmente ao quadrado o raio da roda.

\begin{equation}
I = \frac{m}{2} r^2
\label{eq:Inercia}
\end{equation}

A relação entre a massa da roda de reação com a massa do satélite influencia diretamente na forma como o controle é feito. Como dito anteriormente, quanto maior a massa da roda de reação, e consequentemente a inércia dele, maior a capacidade de atuação. Porém, dada a limitação de espaço hábil dentro do CubeSat, não é possível projetar uma roda de reação com raio grande. Para compensar, a roda utilizada deverá ter uma massa mais elevada, e a forma de conseguir isso com dimensões limitadas é utilizando materiais mais densos. Nesse caso, a roda foi projetada considerando aço, como mostrado a seguir na Figura \ref{fig:RW}.

\begin{figure}[th]
	\caption{Roda de reação.}
	\centering
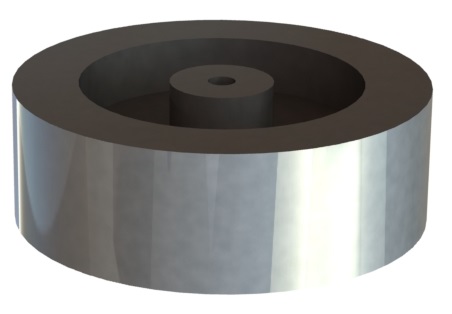
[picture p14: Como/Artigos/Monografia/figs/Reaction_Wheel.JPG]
	
	
	\begin{small}
		FONTE: Arquivo dos autores.
	\end{small}
	\label{fig:RW}
\end{figure}

Por causa da forma como o motor é preso no suporte, foi necessário um pequeno rasgo na roda de reação com o objetivo de evitar que as cabeças dos parafusos interferissem na roda de reação, como mostrado nas folhas do projeto no Apêndice \ref{ap:RW}.

Apesar da roda projetada ser cilíndrica, ela não possui a mesma seção para toda sua extensão, e a Equação \ref{eq:Inercia} se aplica a corpos cilíndricos homogêneos. Para o cálculo correto da inercia, aplica-se a Equação \ref{eq:Inercia} para cada seção e então se aplica a equação \ref{eq:Inetot}.

\begin{equation}
I_{total} = \sum\nolimits I_{1} + I_{2} + I_{3}
\label{eq:Inetot}
\end{equation}

Serão usadas três rodas de reação, uma para cada motor. Elas foram usinadas em aço 1020, em um torno CNC. O peso delas ficou igual a 46g. A Inércia, portante, ficou igual a 57,44gcm$^{2}$. A inércia do rotor do motor é igual a 3,84gcm$^{2}$ (dado extraído do manual do motor, no Anexo \ref{an:MM}. Portanto, a inércia do conjunto ($I_{r}$) é igual a 61,28gcm$^{2}$ (ou 6,128$\cdot$10$^{-6}$kgm$^{2}$).

\subsection{Suporte do motor}

Para suportar o motor, foi desenvolvido um protótipo genérico obedecendo as furações dos motores e o espaço para o eixo para a fixação dos mesmos ao suporte e dele à placa de circuito eletrônico do CubeSat, como mostrado nas folhas do projeto no Apêndice \ref{ap:MS}. Esse suporte foi feito com altura de 10mm da superfície inferior do motor até a placa de circuito eletrônico para que não atrapalhasse o posicionamento dos componentes, como mostrado na Figura \ref{fig:MS} a seguir. Para atender aos requisitos de peso, o suporte foi projetado em alumínio.

\begin{figure}[th]
	\caption{Suporte do motor.}
	\centering
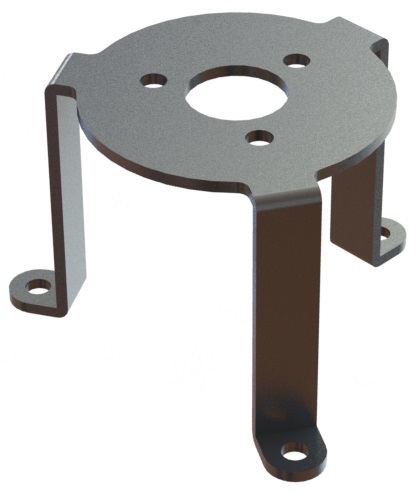
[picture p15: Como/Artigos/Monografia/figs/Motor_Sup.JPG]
	
	
	\begin{small}
		FONTE: Arquivo dos autores.
	\end{small}
	\label{fig:MS}
\end{figure}

\newpage

São usados três suportes, um para cada motor. Eles foram fabricados com chapas de alumínio de 1mm de espessura através de uma máquina de corte a laser e então dobrados. O peso ficou igual a 2,3g.

\subsection{Estrutura mecânica}

A estrutura mecânica do CubeSat foi projetada seguindo os padrões indicados pela Cal Poly \cite{CalPoly}. O projeto foi feito pelo Núcleo de Sistemas Eletrônicos Embarcados (NSEE) da Mauá, que é responsável pelo desenvolvimento do CubeSat Mauá, sendo de nossa responsabilidade apenas o sistema de controle de atitude do satélite. O modelo básico sobre o qual o trabalho se desenvolveu é mostrado a seguir apenas com a estrutura mecânica em si a mostra na Figura \ref{fig:Frame}. %As folhas do projeto da estrutura mecânica se encontram no Anexo \ref{an:MS}.

\begin{figure}[th]
	\caption{Estrutura do CubeSat.}
	\centering
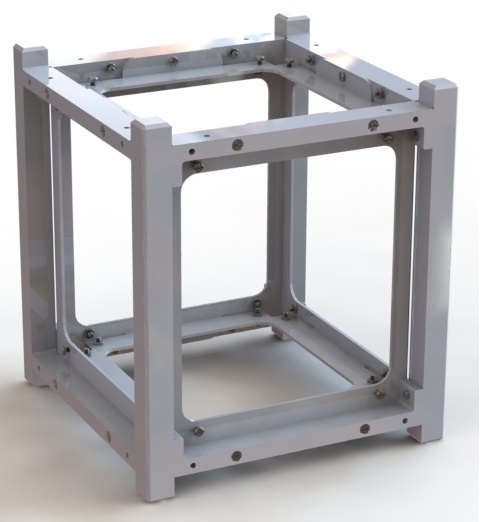
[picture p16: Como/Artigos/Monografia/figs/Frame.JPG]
	
	
	\begin{small}
		FONTE: Arquivo dos autores.
	\end{small}
	\label{fig:Frame}
\end{figure}

\newpage

A estrutura mecânica é composta por uma estrutura principal, responsável por dar a forma e a sustentação do CubeSat e uma estrutura interna, responsável pela fixação das placas eletrônicas, ambas mostradas na Figura \ref{fig:Frame}. Há também chapas de fechamento externas que fecham e protegem o CubeSat, como mostrado a seguir na Figura \ref{fig:FrameFull}.

\begin{figure}[th]
	\caption{CubeSat montado.}
	\centering
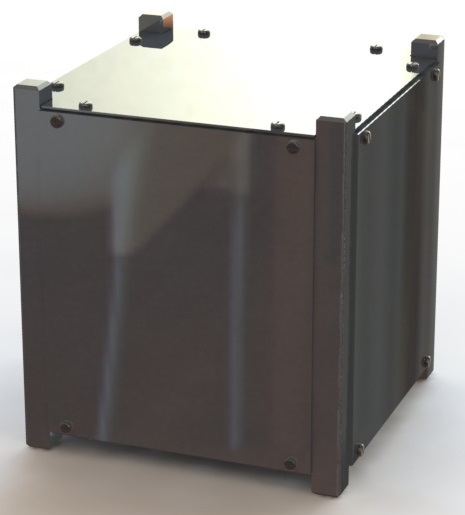
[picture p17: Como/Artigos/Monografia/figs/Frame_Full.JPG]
	
	
	\begin{small}
		FONTE: Arquivo dos autores.
	\end{small}
	\label{fig:FrameFull}
\end{figure}

\newpage

A Tabela \ref{tab:MatMec} a seguir mostra quais os materiais necessários para a construção da estrutura mecânica do CubeSat. As folhas de projeto delas estão no Anexo \ref{an:MS}. Os elementos de fixação utilizados (inclusive os usados para a fixação das placas eletrônicas e suportes dos motores) também estão descritos na Tabela \ref{tab:MatMec}.

\begin{table}[h]
	\caption{Materiais para construção da estrutura mecânica do CubeSat.}
		\centering
	\begin{tabular}{|c|c|}
		\hline
		\textbf{Componentes} & \textbf{Quantidades} \\ 
		\hline 
		Estrutura Interna Lateral Principal & 2 \\ 
		\hline 
		Estrutura Interna Lateral de Ligação & 4 \\ 
		\hline 
		Estrutura Interna Superior & 2 \\
		\hline 
		Placa Interna Lateral & 8 \\
		\hline 
		Casca Externa Superior & 2 \\ 
		\hline 
		Casca Externa Lateral & 4 \\ 
		\hline 
		Parafuso Cabeça de Panela (Fenda) - M2 x 6mm & 105 \\
		\hline
		Porca Sextavada - M2 & 41 \\
		\hline
	\end{tabular}
	
	\begin{small}
	\vspace{3pt}	
	FONTE: Dos autores.
	\end{small}
	\label{tab:MatMec}
\end{table}

\chapter{Métodos}

Nesta seção, é explicada a metodologia aplicada para atingir os seguinte objetivos:

a)	desenvolver um sistema de controle de atitude para um satélite do tipo CubeSat, utilizando rodas de reação;

b)	desenvolver placas de circuitos eletrônicos que permitam a aquisição de dados de posicionamento, a comunicação entre micro controladores e o controle dos motores;

c)	desenvolver um \textit{firmware} que possa interpretar os dados de posicionamento e efetuar o controle de atitude.

\section{Base de teste}

Para que seja possível testar o CubeSat e avaliar se seu funcionamento é o esperado, foi desenvolvida uma base que fosse capaz de medir sua posição através de um \textit{encoder}.

\subsection{Estrutura}

A estrutura da base foi desenvolvida em alumínio, visando não adicionar influenciar na inércia do sistema. Ela é composta por quatro partes usinadas, desenvolvidas de forma que pudessem ser fabricadas facilmente. A base de teste é mostrada na Figura \ref{fig:ProtoTB}, a seguir.

\begin{figure}[th]
	\caption{Base de teste.}
	\centering
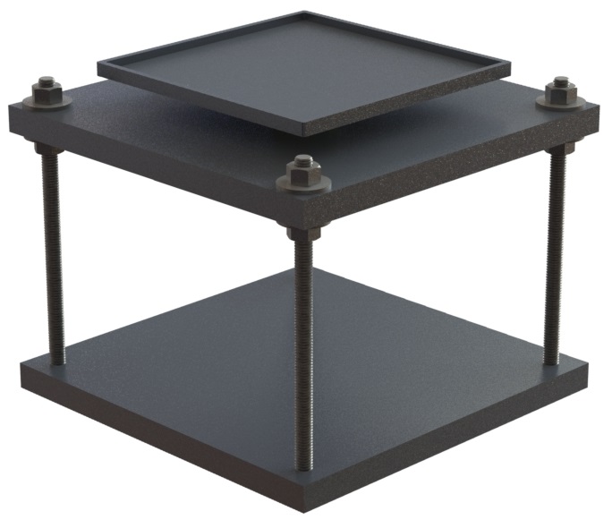
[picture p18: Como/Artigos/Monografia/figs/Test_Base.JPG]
	
	
	\begin{small}
		FONTE: Arquivo dos autores.
	\end{small}
	\label{fig:ProtoTB}
\end{figure}

\newpage

A parte superior foi feita de forma que o CubeSat encaixe nela. Essa parte é acoplada em um eixo, apoiado sobre um rolamento axial de esferas 51100 (SKF, Cajamar, SP), e conectado na outra extremidade a um \textit{encoder}. O rolamento fica apoiado sobre o restante da estrutura que serve tanto para sustentar todo o sistema quanto dar apoio ao \textit{encoder} e à placa que adquire seus dados. As hastes de sustentação da estrutura são barras roscadas M6, que permitem um nivelamento da base sobre qualquer superfície, garantindo que a medição fique livre de interferências. A seguir, na Tabela \ref{tab:MatTB}, a lista de materiais necessários para fabricação e montagem da base de testes.

\begin{table}[h]
	\caption{Materiais para construção da estrutura mecânica da base de testes do CubeSat.}
		\centering
	\begin{tabular}{|c|c|}
		\hline
		\textbf{Componentes} & \textbf{Quantidades} \\ 
		\hline 
		Suporte do CubeSat & 1 \\ 
		\hline 
		Eixo & 1 \\
		\hline
		Base Superior & 1 \\ 
		\hline 
		Base Inferior & 1 \\
		\hline 
		Barra Roscada - M6 x 120mm & 4 \\
		\hline 
		Arruela - M6 & 8 \\ 
		\hline 
		Porca Sextavada - M6 & 8 \\ 
		\hline 
		Rolamento Axial - SKF 51100 & 1 \\
		\hline
	\end{tabular}
	
	\begin{small}
	\vspace{3pt}	
	FONTE: Dos autores.
	\end{small}
	\label{tab:MatTB}
\end{table}

O rolamento foi dimensionado de forma que tivesse uma vida virtualmente infinita (muito grande), mas que não fosse muito grande para não influenciar na inércia do sistema. O rolamento mencionado anteriormente possui diâmetro interno de 10mm, o menor disponível. Para verificar sua vida útil, foi usada a Equação \ref{eq:RolVida} a seguir \cite{ProjMaq}.

\begin{equation}
L_{h} = \frac{ \left( \frac{C}{P} \right)^{p} 10^{6}}{\frac{\omega \cdot 60^{2}}{2 \pi}}
\label{eq:RolVida}
\end{equation}

Onde L$_{h}$ é a vida em horas, C (N) é a classificação de carga básica dinâmica do rolamento, P (N) é a força aplicada sobre ele, p é o coeficiente de ajuste de acordo com o tipo de rolamento e $\omega$(rad/s) é a velocidade angular imposta sobre o rolamento.

Considerando que o peso do CubeSat é de 0,631kg, C é igual a 9950N, p é igual a 3 e a velocidade de rotação média de um CubeSat é aproximadamente 4,8rad/s, esses valores são substituídos e calculados, resultando em:

%\begin{equation}
\begin{center}
$L_{h} = \frac{ \left( \frac{9950}{0,639 \cdot 9,807 } \right)^{3} 10^{6}}{\frac{4,8 \cdot 60^{2}}{2 \pi}} \Longrightarrow Lh = 1,512 \cdot 10^{12} h$
\end{center}
%\label{eq:RolVidaRes}
%\end{equation}

Este alto valor de horas mostra que a vida do rolamento é de fato infinita, principalmente quando se considera que o rolamento não trabalhará com rotações completas sempre. Na maioria dos casos, dará apenas frações de voltas.

Para o dimensionamento das barras roscadas, foi-se adotado que seriam de tamanho M6 (6mm de diâmetro), com o objetivo de prender o sistema de maneira firme, mas que pudesse ser ajustado no caso de superfícies desniveladas. Para garantir que elas suportariam, foi feito um teste de flambagem onde se usou a Equação \ref{eq:Flamb} a seguir \cite{ProjMaq}.

\begin{equation}
d_{h} = \sqrt[4]{ \frac{64 \cdot Cs \cdot \lambda^{2} \cdot Fp \cdot \varphi }{ \pi^{3} \cdot E } }
\label{eq:Flamb}
\end{equation}

Onde Cs é o coeficiente de segurança (adotado como 5), $\lambda$ é o coeficiente de flambagem que, no caso, equivale ao dobro do comprimento da barra já que ela é engastada na base, F$_{p}$ (N) é a Força de projeto, $\varphi$ é o fator de ajuste (adotado como 1,5) e E (MPa) é o módulo de elasticidade do material, no caso um aço inoxidável com módulo igual a 193 GPa. No caso da Força, como a base é simétrica vertical e horizontalmente, o centro de massa fica equidistante dos quatro apoios. A força aplicada então é dividida igualmente por quatro:

%\begin{equation}
\begin{center}
$F_{p} = \frac{1,310 \cdot 9,807}{4} = 3,212 N$
\end{center}
%\label{eq:Fp}
%\end{equation}

Substituindo os valores na Equação \ref{eq:Flamb}, obtemos:

%\begin{equation}
\begin{center}
$d_{h} = \sqrt[4]{ \frac{64 \cdot 5 \cdot 240^{2} \cdot 3,212 \cdot 1,5 }{ \pi^{3} \cdot 210000 } } \Longrightarrow dh = 1,922 mm$
\end{center}
%\label{eq:FlambRes}
%\end{equation}

Como o eixo adotado possui diâmetro de 6mm, ele é maior que o diâmetro mínimo necessário para suportar a carga e portanto não ocorre flambagem.

Os desenhos de projeto das partes da base estão no Apêndice \ref{ap:TB}. A Figura \ref{fig:ProtoTBOK}, a seguir, mostra como ficou a base de teste.

\begin{figure}[th]
	\caption{Base de teste pronta}
	\centering
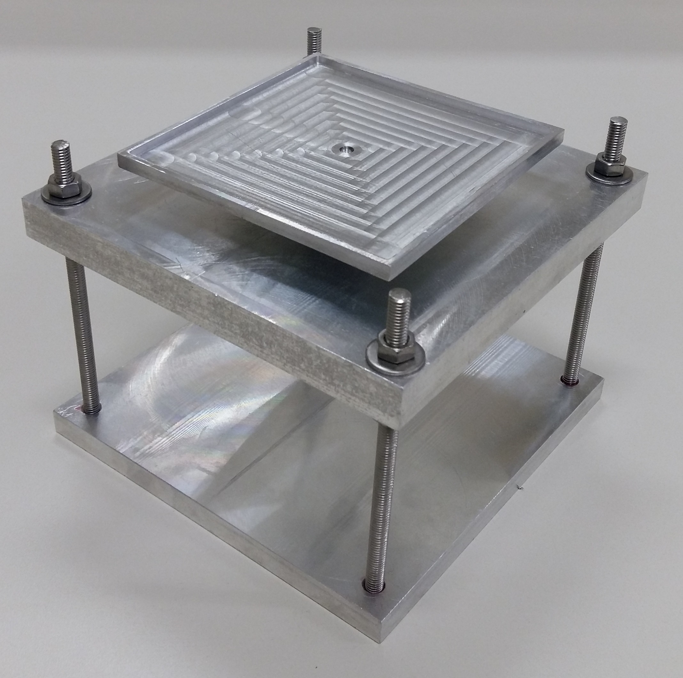
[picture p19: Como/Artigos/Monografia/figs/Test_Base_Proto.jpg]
	
	
	\begin{small}
		FONTE: Arquivo dos autores.
	\end{small}
	\label{fig:ProtoTBOK}
\end{figure}

\newpage

\subsection{Encoder}

\section{Modelagem e controle}

A modelagem do CubeSat foi feita para que pudessem ser conhecidas as equações que regem o sistema como um todo. As equações se resumem nas equações de dinâmica da roda de reação junto do motor (subsistema) e na dinâmica do CubeSat (sistema).

\subsection{Roda de reação e motor}

Ao aplicar uma tensão V (V) em um motor elétrico, uma corrente i (A) passará pelos enrolamentos dele e será convertida em um torque mecânico T$_{m}$ (kgm$^{2}$/s$^{2}$). No motor, há uma resistência R ($\Omega$) devido aos enrolamentos das bobinas. É nessas bobinas que a corrente induz um campo magnético que força o eixo do motor a girar. Isso gera uma tensão contra-eletromotriz V$_{emf}$ (V), que é mostrada na Equação \ref{eq:Tens}.

\begin{equation}
V = i R + V_{emf}
\label{eq:Tens}
\end{equation}

A relação de um motor com imã permanente entre a corrente, o torque T$_{m}$ (Nm) e a constante de torque k$_{T}$ (Nm/A) é descrita na Equação \ref{eq:Torq},  .

\begin{equation}
T_{m} = k_{T} i
\label{eq:Torq}
\end{equation}

A queda de tensão no motor resulta em uma perda de potência. Essa perda costuma ser pequena (e portanto desprezada) caso o motor esteja em boas condições e sem nenhum defeito. O V$_{emf}$ pode ser descrito como na Equação \ref{eq:Vemf}, onde k$_{T}$ e k$_{E}$ (Vs/rad) são o mesmo para um motor com 100\% de eficiência.

\begin{equation}
V_{emf} = k_{T} \omega_{r} = k_{E} \omega_{r}
\label{eq:Vemf}
\end{equation}

Aproveitando a equação de dinâmica da roda de reação, temos a Equação \ref{eq:Tm}, onde $I_{r}$ é o total de inércia do motor junto da roda de reação, B é o coeficiente de atrito viscoso e $\dot{\omega}_{r}$ é a aceleração angular.

\begin{equation}
T_{m} = I_{r} \dot{\omega}_{r} + B \omega_{r}
\label{eq:Tm}
\end{equation}

A Equação \ref{eq:Tens} é substituída na equação \ref{eq:Torq} e substituindo o $V_{emf}$ pela equação \ref{eq:Vemf}, obtemos uma expressão que é igual à Equação \ref{eq:Tm}, como mostrado a seguir:

\begin{align}
	T_{m} & = k_{T} i \nonumber \\
	& = k_{T} \frac{V - V_{emf}}{R} \nonumber \\
	& = k_{T} \frac{ V - k_{T} \omega_{r} }{R} = I_{r} \dot{\omega}_{r} + B \omega_{r}
\label{eq:Subst}
\end{align}

Reescrevendo:

\begin{equation}
I_{r} \dot{\omega}_{r} + \left( B + \frac{k_{T}^{2}}{R} \right) \omega_{r} = \frac{k_{T}}{R} V \nonumber
\label{eq:ReWrite}
\end{equation}

Aplicando então a transformada de Laplace e isolando os termos de saída sobre entrada, obtém-se:

\begin{equation}
\frac{\Omega_{r}(s)}{V(s)} = \frac{\frac{1}{B R + k_{T}}}{\frac{I_{r} R}{B R + k_{T}^{2}} s +1}
\label{eq:Lap}
\end{equation}

Da Equação \ref{eq:Lap}, é possível observar que o valor do denominador e o que multiplica o s são constantes. Portanto, a equação pode ser reescrita da seguinte forma:

\begin{equation}
\frac{\Omega_{r}(s)}{V(s)} = \frac{k_{r}}{\tau_{r} s +1}
\label{eq:RWDM}
\end{equation}

Onde $k_{r}$ e $\tau_{r}$ são constantes. Portanto, a Equação \ref{eq:RWDM} é o modelo dinâmico do conjunto roda de reação e motor escritos \cite{Ericksson}.

Para fazer a equação de controle do sistema modelado anteriormente, foi consideradoo seguinte funcionamento: a entrada do sistema é um \textit{set point} de velocidade angular que é subtraído pela realimentação, gerando um erro que entra no controlador K$_{r}$ e sai como uma tensão (V), que por sua vez entra na planta G$_{r}$ e resulta em uma velocidade angular, fechando a malha. Isso tudo é mostrado a seguir, na Figura \ref{fig:Diagram}.

\begin{figure}[th]
	\caption{Diagrama de blocos do sistema motor e roda de reação.}
	\centering
	
	
	\begin{small}
		FONTE: Arquivo dos autores.
	\end{small}
	\label{fig:Diagram}
\end{figure}

Observando a equação da planta, chegou-se a conclusão de que um controlador Proporcional-Integral (PI) seria o mais adequado. Portanto, tomou-se como base a Equação \ref{eq:PI} a seguir:

\begin{equation}
K_{r}(s) = \frac{k_{cr}(s+z_{r0})}{s}
\label{eq:PI}
\end{equation}

Onde k$_{cr}$ é o ganho do controlador e z$_{r0}$ é o zero do controlador. Para calcular os valores das constantes, precisou-se determinar o valor de k$_{r}$ e $\tau_{r}$, dependentes de constantes já conhecidas: I$_{r}$ = 6,128$\cdot$10$^{-6}$ kgm$^{2}$, R = 23,9 $\Omega$, k$_{T}$ = 11,3$\cdot$10$^{-3}$ Nm/A e B = 4,9$\cdot$10$^{-6}$ kgm$^{2}$/s. A inércia foi obtida através do \textit{software} de simulação SolidWorks 2013 e validados comparando a massa obtida através dele com a massa real. A resistência e a constante de torque foi obtida no catálogo do motor, no Anexo \ref{an:MM}. Já o coeficiente de atrito viscoso foi estimado com referência à testes realizados no INPE \cite{Carrara}. Com estes valores, calculou-se que k$_{r}$ = 87,588 e $\tau_{r}$ = 0,598.

Com estes valores, o controlador foi projetado de forma que o zero "cancelasse" o polo da planta, portanto: z$_{r0}$ = 0,598. Já o ganho foi igualado a 2 dividido pelo ganho da planta, para que o ganho final seja igual a 2. Logo:

\begin{equation}
k_{cr} = 2/87,588 \Longrightarrow k_{cr} = 0,022834 \nonumber
\label{eq:kcr}
\end{equation}

Substituindo os valores encontrados na Equação \ref{eq:PI}, obtemos:

\begin{equation}
K_{r}(s) = \frac{0,022834(s+0,598)}{s}
\label{eq:PI_calc}
\end{equation}

Discretizando a Equação \ref{eq:PI_calc} no \textit{software} matemático MATLAB com período de amostragem T =  s, através do método de Tustin, obteve-se a equação:

\begin{equation}
K_{r}(z) = \frac{0,023107314300773-0,022561042095081}{z-1}
\label{eq:PI_disc}
\end{equation}

Da Equação \ref{eq:PI_disc}, obtém-se a equação de diferenças implementada no microcontrolador:

\begin{equation}
u_{rk} = u_{rk-1} + 0,023107314300773e_{rk} - 0,022561042095081e_{rk-1}
\label{eq:PI_eqdif}
\end{equation}

O elevado número de casas decimais é devido ao fato dos valores serem muito próximos entre si, podendo levar a uma diferença de erros muito pequena, causando um erro estacionário.

\subsection{CubeSat}

O satélite será afetado pela rotação dos conjuntos motor - roda de reação. Pela terceira Lei de Newton, o momento torçor que age no conjunto reage no sistema, criando um momento torçor de igual intensidade no sentido contrário, como mostrado na Equação \ref{eq:Newton}.

\begin{equation}
M_{r} = M
\label{eq:Newton}
\end{equation}

Onde $M_{r}$ é o momento torçor do conjunto e M é o momento torçor do sistema. Pode-se considerar que a dinâmica do sistema é composta unicamente por uma inércia sujeita a um torque resistivo causado por um coeficiente de atrito seco com o ar. Ou seja, $M_{r}$ é causado pela inércia da roda de reação somada com a inércia do rotor do motor $I_{r}$ multiplicados pela aceleração angular $\dot{\omega}_{r}$. Enquanto M é a inércia do satélite I multiplicado pela aceleração do sistema $\dot{\omega}$,  decrescido do coeficiente de atrito C multiplicado pela velocidade angular $\omega$. Isso é demonstrado a seguir, na Equação \ref{eq:Moment}.

\begin{equation}
I_{r}\dot{\omega}_{w} = I\dot{\omega} - C\omega
\label{eq:Moment}
\end{equation}

Reorganizando a equação, aplicando Laplace e isolando os termos de entrada (velocidade da roda de reação) sobre a saída (velocidade do satélite), obtemos a Equação \ref{eq:LapMom} mostrada a seguir.

\begin{equation}
\frac{\Omega(s)}{\Omega(s)_{r}} = \frac{I_{r}s}{Is - C}
\label{eq:LapMom}
\end{equation}

Ao colocar um integrador na saída do sistema, obtemos a posição dele, que é a variável a ser controlada. Isso significa que a Equação \ref{eq:SDM} a seguir é o modelo dinâmico do sistema.

\begin{equation}
\frac{\Theta(s)}{\Omega(s)_{r}} = \frac{I_{r}}{Is - C}
\label{eq:SDM}
\end{equation}

%\includegraphics[width=.8\linewidth]{untitled.eps}

% ----------------------------------------------------------
% PROTÓTIPO 
% ----------------------------------------------------------
\chapter{Protótipo}

Nesta seção está a descrição de como foi feito o protótipo do CubeSat. Desde os elementos individuais, como as rodas de reação, suportes dos motores, estruturas mecânicas e placas eletrônicas, até o CubeSat como um todo.

\section{Rodas de reação}

Os protótipos das rodas de reação foram feitos em aço 1020 em um torno CNC (Baron-Max, Taiwan) pela empresa Rudloff. A seguir, na Figura \ref{fig:ProtoRW}, uma imagem de como ficaram.

\begin{figure}[th]
	\caption{Modelo das rodas de reação.}
	\centering
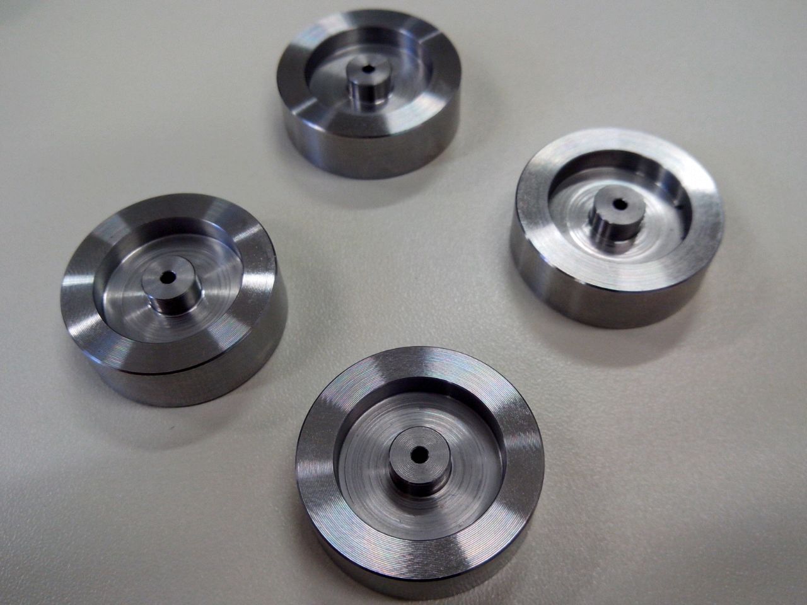
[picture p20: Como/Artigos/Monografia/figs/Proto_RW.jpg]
	
	
	\begin{small}
		FONTE: Arquivo dos autores.
	\end{small}
	\label{fig:ProtoRW}
\end{figure}

\section{Suporte do motor}

Para uma pré validação do projeto do suporte do motor, foi feito um modelo impresso em uma impressora 3D (Cliever, Porto Alegre, RS), como mostrado a seguir na Figura \ref{fig:ProtoMSP}. Esse modelo foi usado para garantir o batimento dos furos do suporte com os do motor.

\begin{figure}[th]
	\caption{Protótipo em resina do suporte do motor.}
	\centering
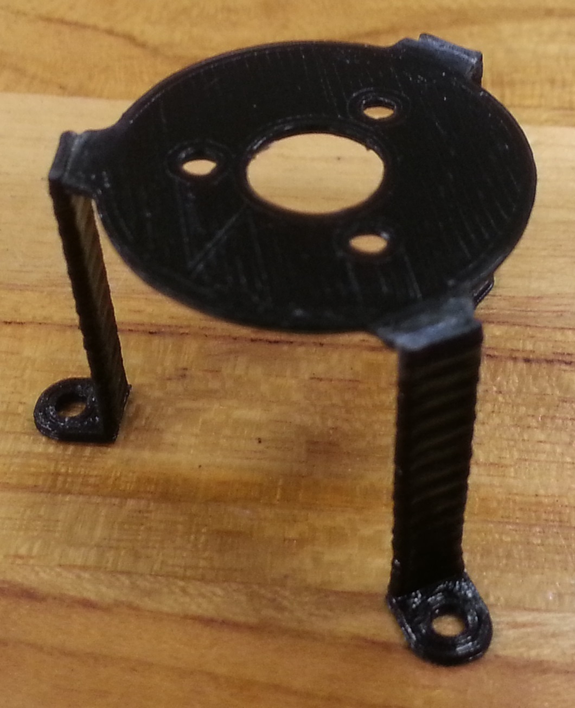
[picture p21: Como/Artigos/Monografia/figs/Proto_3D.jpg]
	
	
	\begin{small}
		FONTE: Arquivo dos autores.
	\end{small}
	\label{fig:ProtoMSP}
\end{figure}

\newpage

Uma vez validado, foi mandado fazer um modelo em alumínio, através do corte por máquina de corte laser (Bystronic, Suíça) e dobra, através de uma dobradeira (Bystronic, Suíça). Esse modelo é mostrado a seguir, na Figura \ref{fig:ProtoMS}.

\begin{figure}[th]
	\caption{Modelo em metal do suporte do motor.}
	\centering
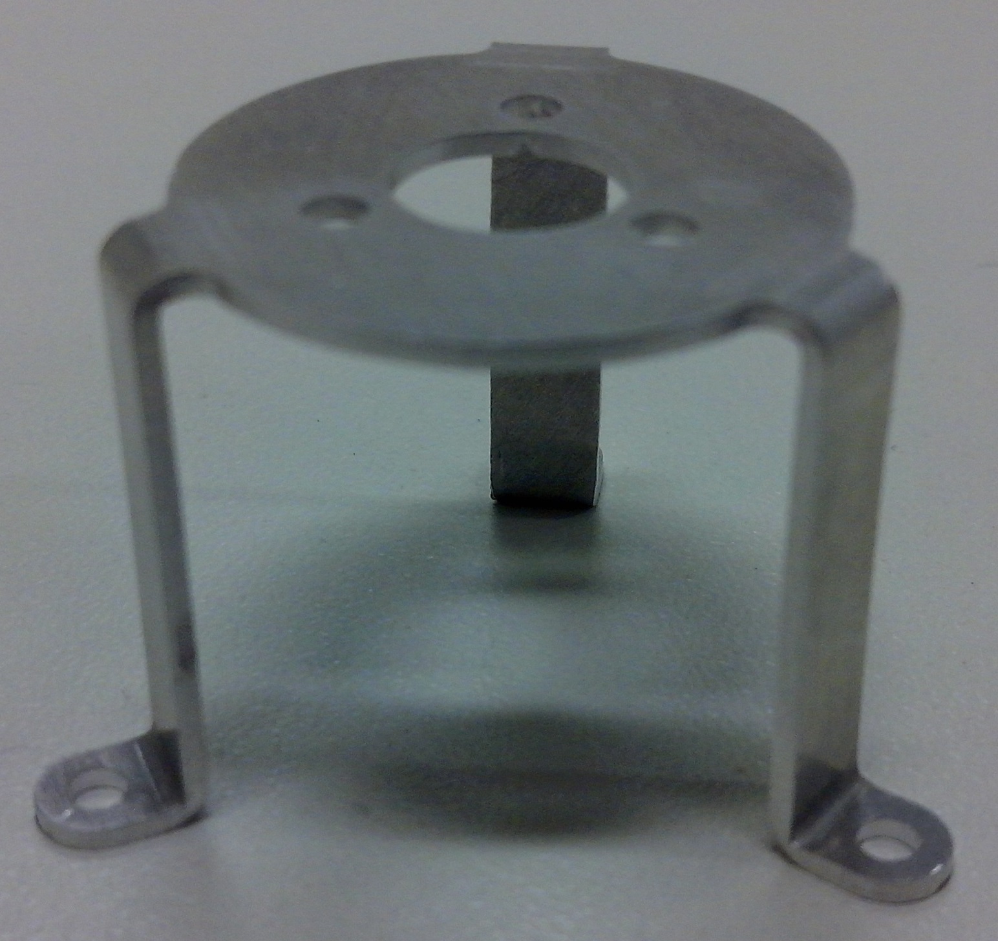
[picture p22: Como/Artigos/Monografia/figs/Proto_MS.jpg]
	
	
	\begin{small}
		FONTE: Arquivo dos autores.
	\end{small}
	\label{fig:ProtoMS}
\end{figure}

\section{Estrutura mecânica}

Um primeiro protótipo da estrutura mecânica foi fabricado na oficina mecânica da Mauá para que pudessem ser feitos os primeiros testes de encaixe, tanto da própria estrutura quanto das placas de circuito eletrônico, inteira em alumínio. A seguir, na Figura \ref{fig:Protoone}, a estrutura montada. Foram deixadas três chapas de fechamento removidas para que fosse possível visualizar o interior do mesmo.

\begin{figure}[ht]
	\caption{Primeiro protótipo do CubeSat com três chapas de fechamento removidas.}
	\centering
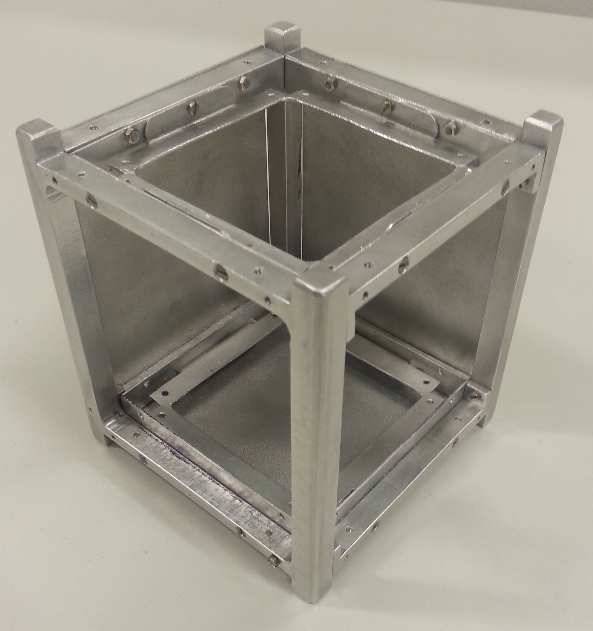
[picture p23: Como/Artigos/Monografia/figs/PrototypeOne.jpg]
	
	
	\begin{small}
		FONTE: Arquivo dos autores.
	\end{small}
	\label{fig:Protoone}
\end{figure}

%\newpage

Posteriormente, foram feitos ajustes nos desenhos em CAD e uma nova versão foi feita. As partes de chapas foram feitas em máquinas de corte laser e dobradas, caso necessário, por uma empresa especializada. As outras partes foram feitas em um centro de usinagem no laboratório de usinagem da Mauá. O modelo finalizado sem as chapas de fechamento é mostrado a seguir, na Figura \ref{fig:ProtoTwo}.

\begin{figure}[th]
	\caption{Versão final da estrutura do CubeSat.}
	\centering
%	\includegraphics[width=0.7\linewidth]{./figs/}
	
	\begin{small}
		FONTE: Arquivo dos autores.
	\end{small}
	\label{fig:ProtoTwo}
\end{figure}

\section{Placas eletrônicas}

% ----------------------------------------------------------
% RESULTADOS E DISCUSSÕES
% ----------------------------------------------------------
\chapter{Resultados e discussões}

% ----------------------------------------------------------
% CONCLUSÕES
% ----------------------------------------------------------
\chapter{Conclusões}

% ----------------------------------------------------------
% REFERÊNCIAS BIBLIOGRÁFICAS
% ----------------------------------------------------------
\bibliography{TCC_Sist_Controle_Atitude}

% ----------------------------------------------------------
% Apêndices
% ----------------------------------------------------------
% Inicia os apêndices
% ---
\begin{apendicesenv}
% Imprime uma página indicando o início dos apêndices
\partapendices
% ---

\chapter{Desenho da placa de controle}

\begin{figure}[th]
	\centering
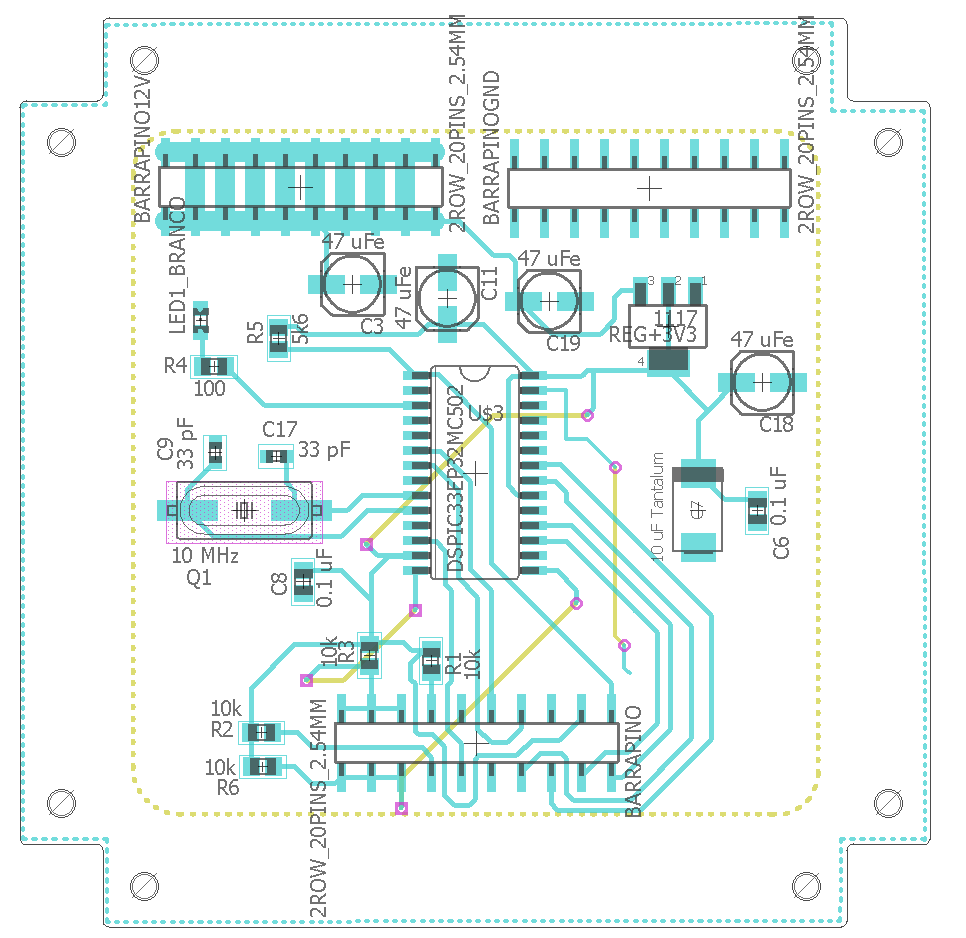
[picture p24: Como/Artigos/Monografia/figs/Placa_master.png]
	
\end{figure}

\label{ap:PMaster}

\chapter{Desenho da placa dos motores}

\begin{figure}[th]
	\centering
	
\end{figure}

\label{ap:PMotor}

\chapter{Desenho da roda de reação}

\includepdf[pages=-]{./pdfs/Cubesat-Reaction-Wheel}

\label{ap:RW}

\chapter{Desenho do suporte do motor}

\includepdf[pages=-]{./pdfs/Cubesat-Struct-Int-Motor-Suport}

\label{ap:MS}

\chapter{Desenho da base de testes}

\includepdf[pages=-]{./pdfs/Testbase-Assembly}
\includepdf[pages=-]{./pdfs/Testbase-Struct-Base-Low}
\includepdf[pages=-]{./pdfs/Testbase-Struct-Base-Top}
\includepdf[pages=-]{./pdfs/Testbase-Struct-Axis}
\includepdf[pages=-]{./pdfs/Testbase-Struct-Base-CubeSat}

\label{ap:TB}

\end{apendicesenv}

% ----------------------------------------------------------
% Anexos
% ----------------------------------------------------------
% Inicia os anexos
% ---
\begin{anexosenv}
% Imprime uma página indicando o início dos anexos
\partanexos
% ---
\chapter{Página do catálogo do motor \textit{brushless} 351100 da Maxon}

\includepdf[pages=-]{./pdfs/351100}

\label{an:MM}

%\chapter{Desenho da estrutura mecânica do CubeSat}

%\label{an:MS}

%\includepdf[pages=-]{./pdfs/Cubesat-Struct-Ext-Shell-Side-1U}
%\includepdf[pages=-]{./pdfs/Cubesat-Struct-Ext-Shell-Top}
%\includepdf[pages=-]{./pdfs/Cubesat-Struct-Int-Frame-Side01}
%\includepdf[pages=-]{./pdfs/Cubesat-Struct-Int-Frame-Side02}
%\includepdf[pages=-]{./pdfs/Cubesat-Struct-Int-Frame-Top}
%\includepdf[pages=-]{./pdfs/Cubesat-Struct-Int-Plate-PCBStructHalf}

\chapter{}

\label{an:}

\end{anexosenv}

\end{document}

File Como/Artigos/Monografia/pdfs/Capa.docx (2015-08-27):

Centro Universitário do Instituto Mauá de Tecnologia
Escola de Engenharia Mauá
Engenharia de Controle e Automação

Augusto Bonangelo Costa
Felipe Ramos de Faria
William Mazi

Sistema de controle de atitude para satélite CubeSat

São Caetano do Sul
2015

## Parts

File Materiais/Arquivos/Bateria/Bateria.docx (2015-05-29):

Bateria:

https://www.robocore.net/modules.php?name=GR_LojaVirtual&prod=659

Especificações:

- Capacidade: 1300mAh
- Tensão: 3S1P / 3 células / 11.1V
- Descarga: 25C constante / 50C por curtos períodos de tempo
- Peso: 119g (incluindo cabo, plug e rótulo)
- Dimensões: 70x34x22mm
- Plug Balanceador: JST-XH
- Plug de Descarga: XT60 (esta bateria é muito potente para um plug menor)

Carregador:

https://www.robocore.net/modules.php?name=GR_LojaVirtual&prod=656

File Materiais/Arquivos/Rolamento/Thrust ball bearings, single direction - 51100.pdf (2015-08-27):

Thrust ball bearings, single direction

Principal dimensions | Basic load ratings | Speed ratings | Designations

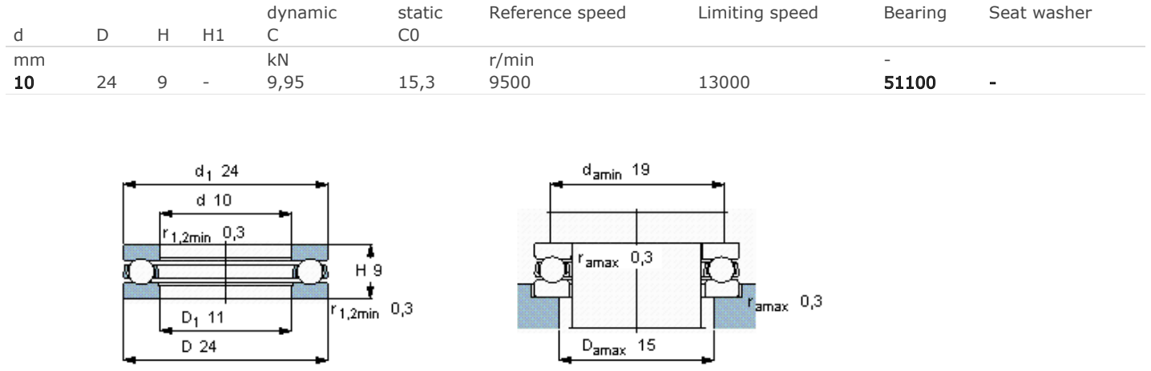
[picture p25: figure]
dynamic; static; Reference speed; Limiting speed; Bearing; Seat washer; r/min

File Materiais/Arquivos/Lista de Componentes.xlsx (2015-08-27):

Descrição | Fabricante | CubeSat Controle
 |  | Quantidade placa motor | Quantidade placa controle
Regulador de tensão REG1117 | TEXAS INSTRUMENTS | 1 | 1
Conector 1-84953-1 | TE CONNECTIVITY | 1
Resistor shunt 0.5 OHM, 1W, 1% | VISHAY | 1
Amplificador operacional LMV358 | TEXAS INSTRUMENTS | 1
Circuito integrado DRV8313 | TEXAS INSTRUMENTS | 1
Microcontrolador dsPIC33EP32MC502 | Microchip | 1 | 1
Capacitor eletrolítico 47 uF |  | 4 | 4
Capacitor eletrolítico 10 uF |  | 1
Capacitor cerêmico 0.1 uF |  | 7 | 2
Capacitor cerêmico 33 pF |  | 5 | 2
Capacitor de tântalo 10 uF |  | 1 | 1
Resistor 100 Ω |  | 2 | 1
Resistor 1k Ω |  | 1
Resistor 3k3 Ω |  | 1
Resistor 4k7 Ω |  | 3
Resistor 5k6 Ω |  | 1 | 1
Resistor 10k Ω |  | 1 | 4
Resistor 62k Ω |  | 3
Resistor 150k Ω |  | 3
Led branco |  | 1 | 1
Led verde |  | 1
Cristal 10 MHz |  | 1 | 1
Barra de pino 20x2 |  | 1 | 3
Beteria 1300 mAh | Turnigy | 1
Conector XT60 fêmea | TGY | 1
Módulo bluetooth HM-10 | JNHuaMao Technology Company | 1
Cabinho jumper |  | 60

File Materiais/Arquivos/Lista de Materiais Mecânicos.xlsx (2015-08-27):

LISTA DE MATERIAIS MECÂNICOS
COMPONENTES |  | QUANTIDADE | COMPONENTES |  | QUANTIDADE (x4)
ELEMENTOS | SUPORTE DO MOTOR | 6 | FIXAÇÃO | PARAFUSO CABEÇA DE PANELA (FENDA OU PHILLIPS) M2 X 3MM | 20
 | RODA DE REAÇÃO (1.5" x 60 mm) | 5 (1 tarugo)
 | ESTRUTURA INTERNA - TOPO | 2 |  | PARAFUSO CABEÇA DE PANELA (FENDA OU PHILLIPS) M2 X 6MM (suporte) | 20
 | ESTRUTURA EXTERNA - TOPO | 2
 | ESTRUTURA INTERNA - LATERAL | 8 |  | PORCA SEXTAVADA M2 | 20
 | ESTRUTURA EXTERNA - LATERAL | 4 |  | PARAFUSO CABEÇA DE PANELA (FENDA OU PHILLIPS) M2 X 6MM | 450
 | ARMAÇÃO LATERAL TOTAL | 2
 | ARMAÇÃO LATERAL PARCIAL | 4 |  | PORCA SEXTAVADA M2 | 130
TOTAL |  | 28 | TOTAL |  | 60

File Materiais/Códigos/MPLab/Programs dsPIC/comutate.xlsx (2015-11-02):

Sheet: Plan1
Ant Horario
State | OUTPUT1 | OUTPUT2 | OUTPUT3 | HALLA | HALLB | HALLC | # Hall | Horario
6 | Float | High | Low | 0 | 1 | 0 | 2 | 1
1 | High | Float | Low | 1 | 1 | 0 | 6 | 2
2 | High | Low | Float | 1 | 0 | 0 | 4 | 3
3 | Float | Low | High | 1 | 0 | 1 | 5 | 4
4 | Low | Float | High | 0 | 0 | 1 | 1 | 5
5 | Low | High | Float | 0 | 1 | 1 | 3 | 6
Horário
State | OUTPUT1 | OUTPUT2 | OUTPUT3 | HALLA | HALLB | HALLC | # Hall | Horario
6 | Float | High | Low | 0 | 1 | 0 | 2 | 5
5 | Low | High | Float | 0 | 1 | 1 | 3 | 4
4 | Low | Float | High | 0 | 0 | 1 | 1 | 3
3 | Float | Low | High | 1 | 0 | 1 | 5 | 2
2 | High | Low | Float | 1 | 0 | 0 | 4 | 1
1 | High | Float | Low | 1 | 1 | 0 | 6 | 6

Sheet: Plan2
Q1 | HALL R H
Q2 | HALL Y H
Q3 | HALL B H
Q4 | HALL R L
Q5 | HALL Y L
Q6 | HALL B L

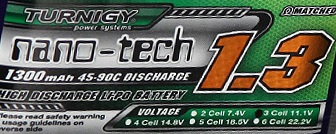
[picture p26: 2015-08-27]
Materiais/Arquivos/Bateria/BatteryLabel.jpg

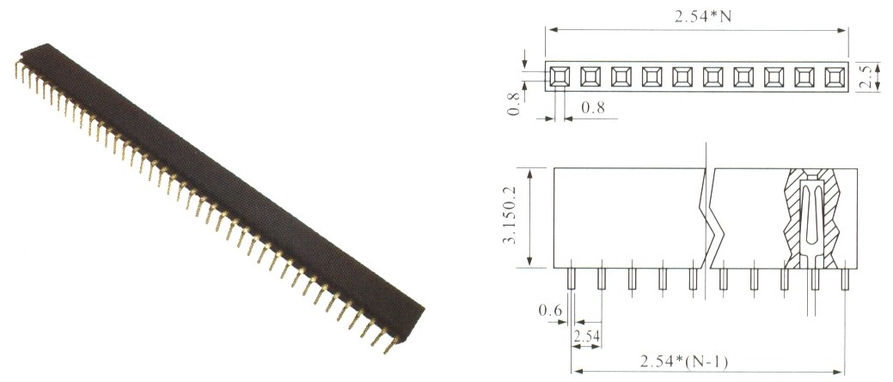
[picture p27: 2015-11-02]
Materiais/Eletrônica/Estudo Medidor de Corrente/Soquete de Barra 1x40 MCI 90°.jpg

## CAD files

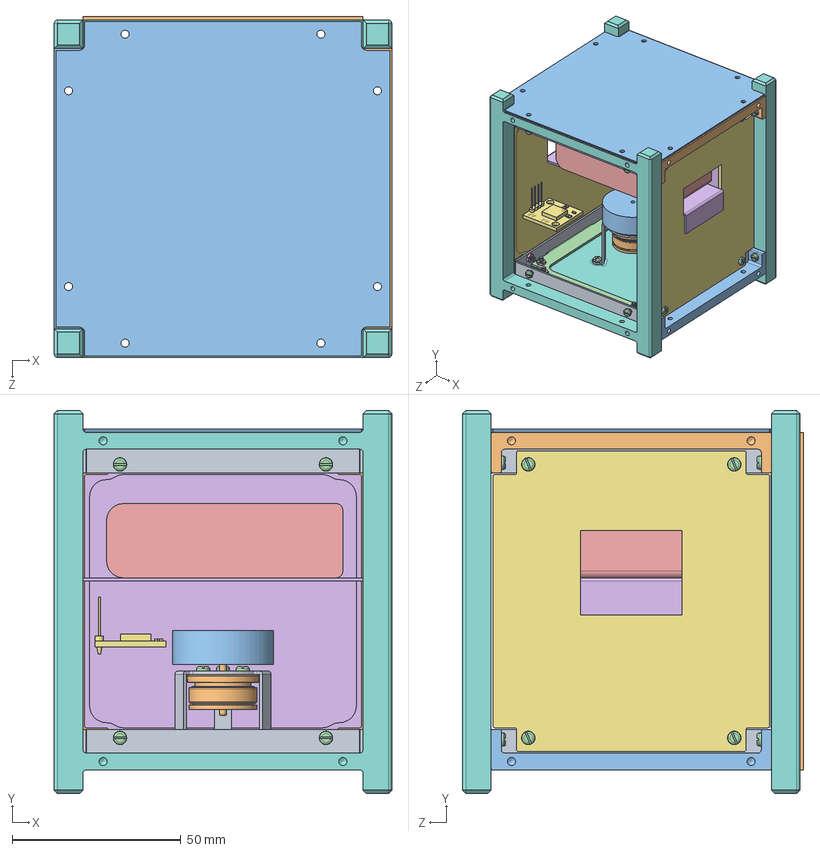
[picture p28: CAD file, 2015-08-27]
Materiais/Mecânica/Controle/CubeSat Eureka.SLDASM
100.0 x 113.5 x 101.0 mm
Suporte Motor
Roda Reação
slotted pan head screw_din x 70
Bateria
Suporte Bateria
Cubesat-Struct-Int-Frame-Side01 x 2
Cubesat-Struct-Int-Plate-PCBStructHalf x 8
Cubesat-Struct-Int-Frame-Side02 x 2
Cubesat-Struct-Int-Frame-Side03 x 2
Cubesat-Struct-Int-Frame-Top x 2
hex thin nut chamfered gradeab_din x 32
Cubesat-PCB-Side-Eureka x 2
Cubesat-PCB-Top-Eureka
hex nut style 1 gradeab_din x 3

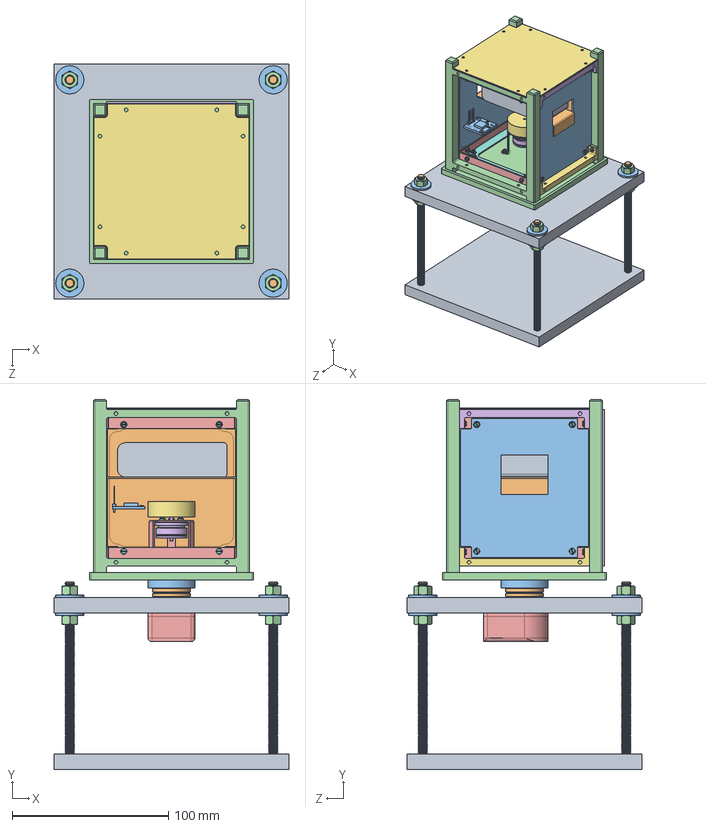
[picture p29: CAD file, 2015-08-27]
Materiais/Mecânica/Base de Teste/Base de Teste.SLDASM
150.0 x 236.5 x 150.0 mm
Base - Top
Eixo
Base CubeSat
Suporte Motor
Roda Reação
slotted pan head screw_din x 70
Bateria
Suporte Bateria
Cubesat-Struct-Int-Frame-Side01 x 2
Cubesat-Struct-Int-Plate-PCBStructHalf x 8
Cubesat-Struct-Int-Frame-Side02 x 2
Cubesat-Struct-Int-Frame-Side03 x 2
Cubesat-Struct-Int-Frame-Top x 2
hex thin nut chamfered gradeab_din x 32
Cubesat-PCB-Side-Eureka x 2
Cubesat-PCB-Top-Eureka
hex nut style 1 gradeab_din x 3
Base - Low
studbolt_din x 4
plain washer 6902 type abc_din x 8
hex nut style 2 gradeab_din x 8
Encoder

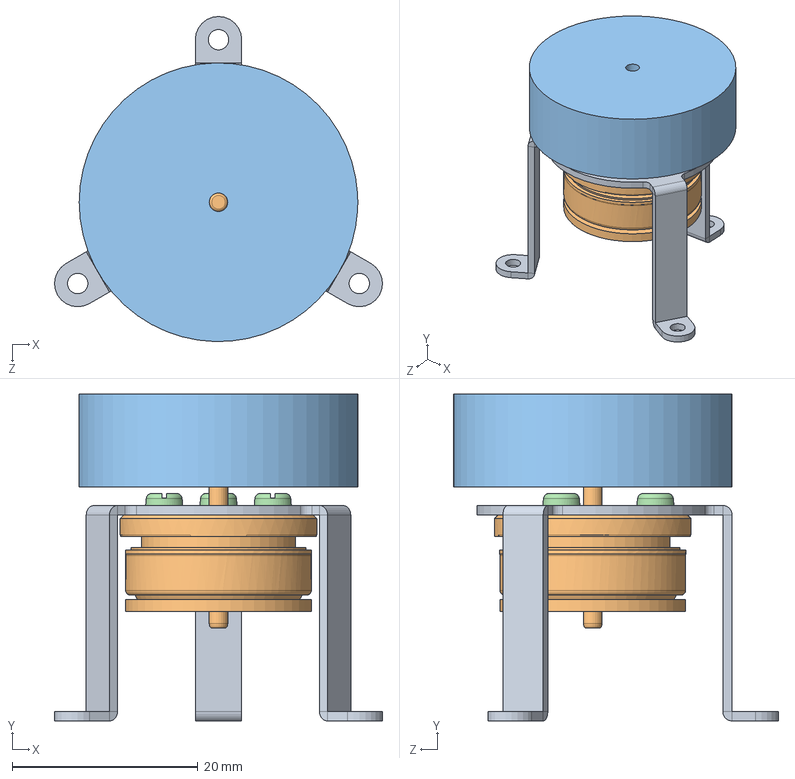
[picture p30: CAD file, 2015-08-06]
Materiais/Mecânica/Controle/Conjunto Motor.SLDASM
35.3 x 35.2 x 35.0 mm
Suporte Motor
Roda Reação
slotted pan head screw_din x 3

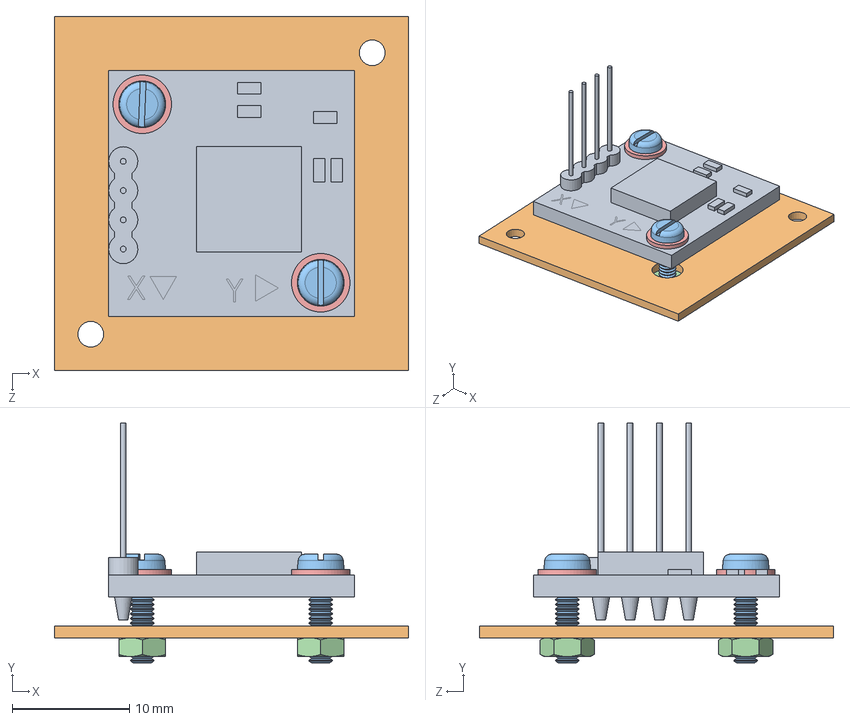
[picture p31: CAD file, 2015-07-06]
Materiais/Mecânica/Controle/Conjunto IMU.SLDASM
30.2 x 20.5 x 30.2 mm
IMU
Suporte IMU
slotted pan head screw_din x 2
hex nut style 1 gradeab_din x 2
plain washer small grade a_din x 2

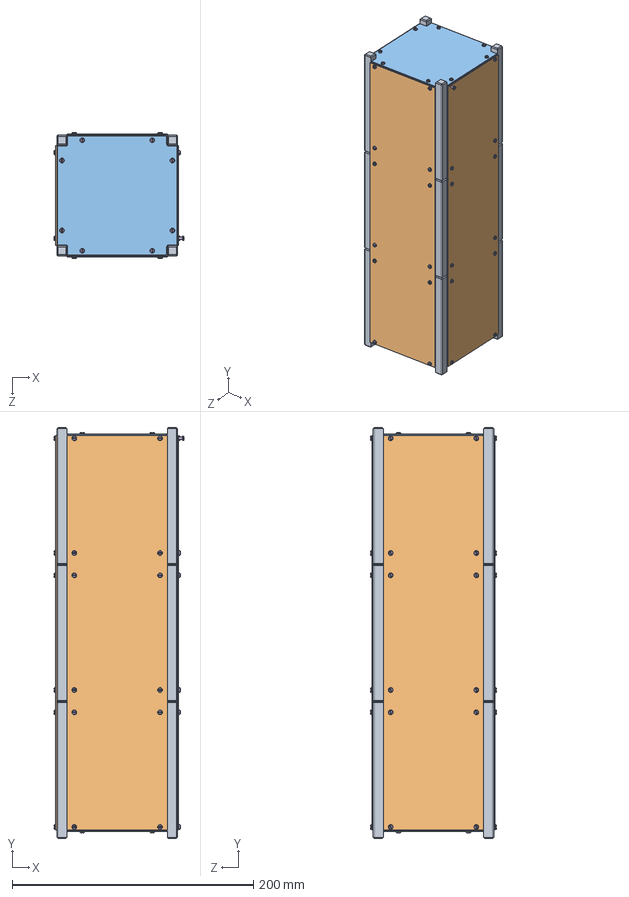
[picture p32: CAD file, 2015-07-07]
Materiais/Mecânica/CubeSat/Cubesat-3U-Assembly.SLDASM
107.6 x 340.5 x 104.6 mm
Cubesat-Struct-Int-Frame-Side01 x 6
Cubesat-Struct-Int-Plate-PCBStructHalf x 24
Cubesat-Struct-Int-Frame-Side02 x 6
Cubesat-Struct-Int-Frame-Side03 x 6
Cubesat-Struct-Int-Frame-Top x 6
slotted pan head screw_din x 256
hex thin nut chamfered gradeab_din x 96
Cubesat-PCB-Side x 6
Cubesat-PCB-Top x 3
Cubesat-Struct-Ext-Shell-Side-3U x 4
Cubesat-Struct-Ext-Shell-Top x 2

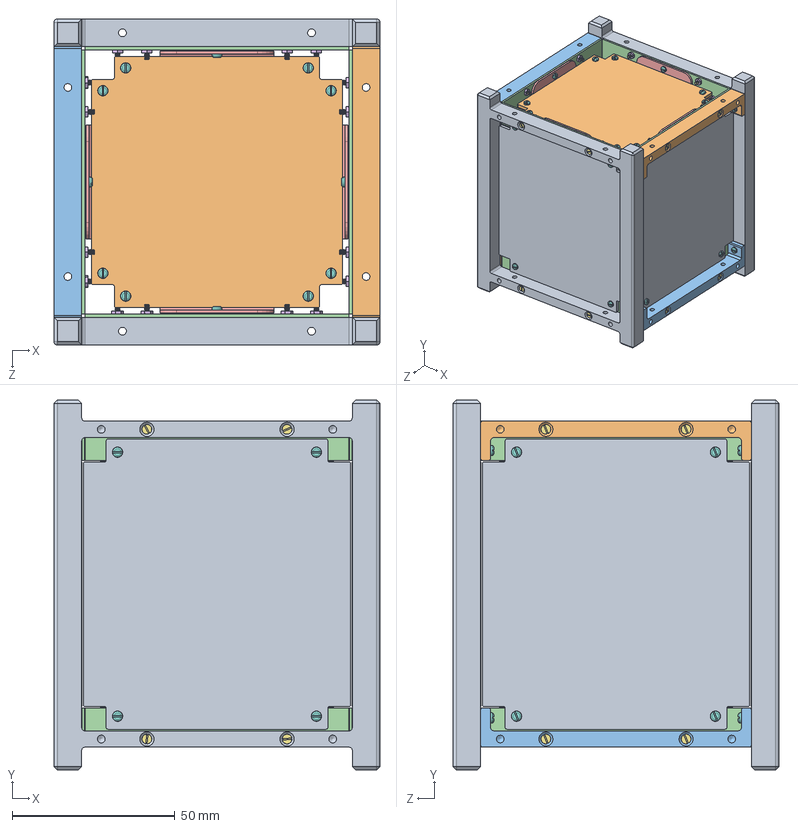
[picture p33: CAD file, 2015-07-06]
Materiais/Mecânica/CubeSat/Cubesat-1U-Assembly.SLDASM
100.0 x 113.5 x 100.0 mm
Cubesat-Struct-Int-Frame-Side01 x 2
Cubesat-Struct-Int-Frame-Side02 x 2
Cubesat-Struct-Int-Frame-Side03 x 2
Cubesat-Struct-Int-Plate-PCBStructHalf x 8
Cubesat-Struct-Int-Frame-Top x 2
hex thin nut chamfered gradeab_din x 32
slotted countersunk flat head screw_din x 16
slotted pan head screw_din x 48
Cubesat-PCB-Side x 4
Cubesat-PCB-Top x 2

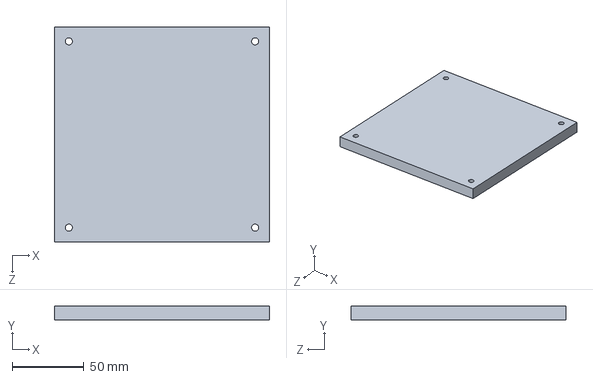
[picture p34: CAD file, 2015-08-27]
Materiais/Mecânica/Base de Teste/Base - Low.SLDPRT
150.0 x 10.0 x 150.0 mm

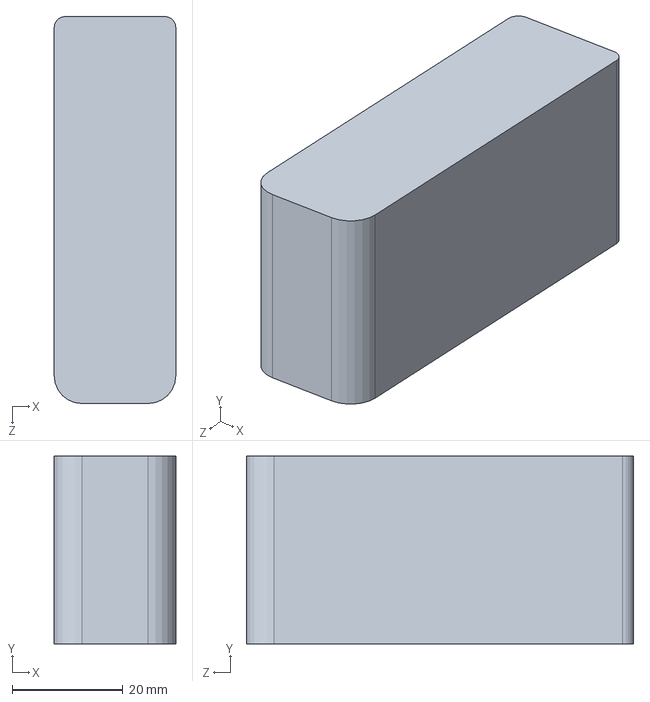
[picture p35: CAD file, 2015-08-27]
Materiais/Mecânica/Controle/Bateria.SLDPRT
22.0 x 34.0 x 70.0 mm

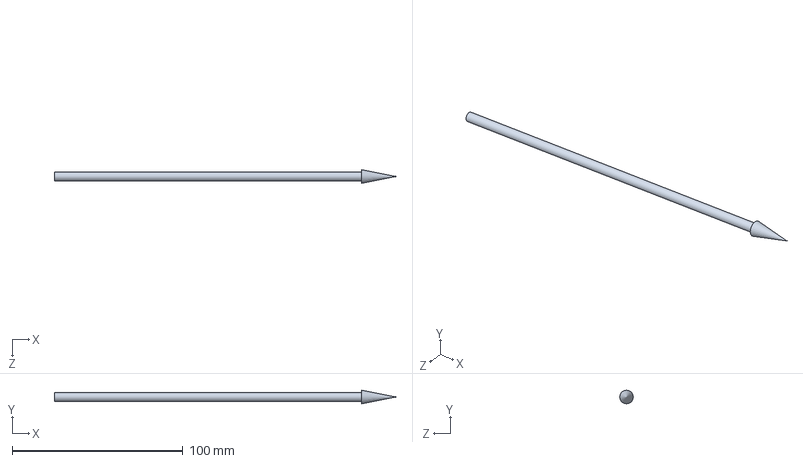
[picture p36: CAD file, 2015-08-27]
Materiais/Mecânica/CubeSat/Axis.SLDPRT
200.0 x 8.00 x 8.00 mm

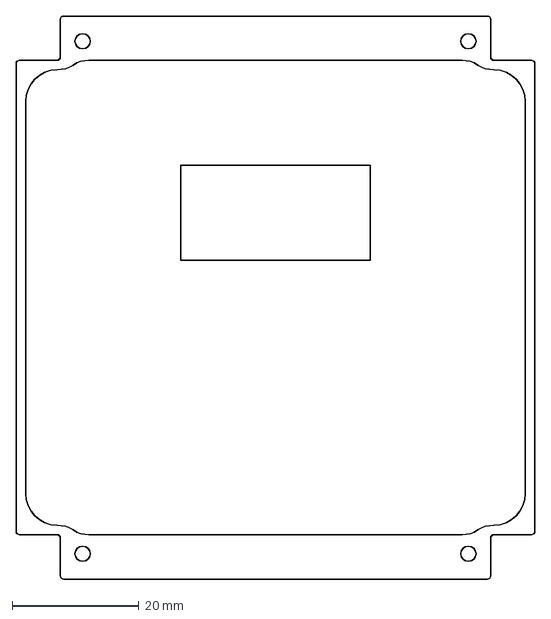
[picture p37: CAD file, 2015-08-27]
Materiais/Mecânica/Fabricação/PCB/Cubesat-PCB-Side-Eureka.dxf
82.0 x 89.0 mm

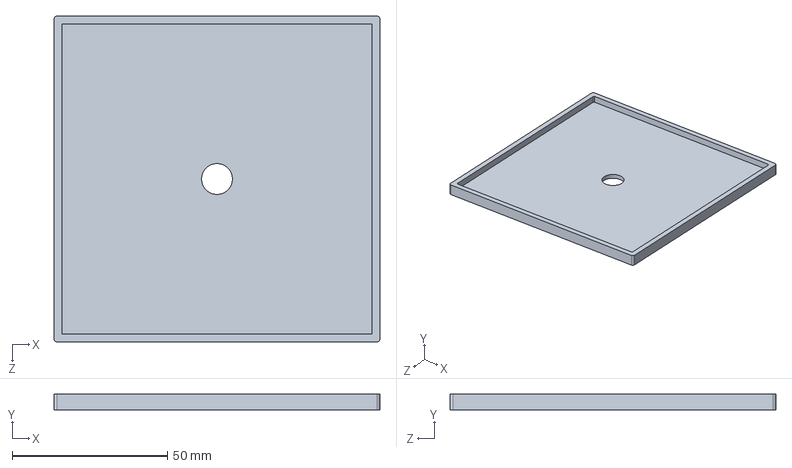
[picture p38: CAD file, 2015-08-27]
Materiais/Mecânica/Base de Teste/Base CubeSat.SLDPRT
105.0 x 5.00 x 105.0 mm

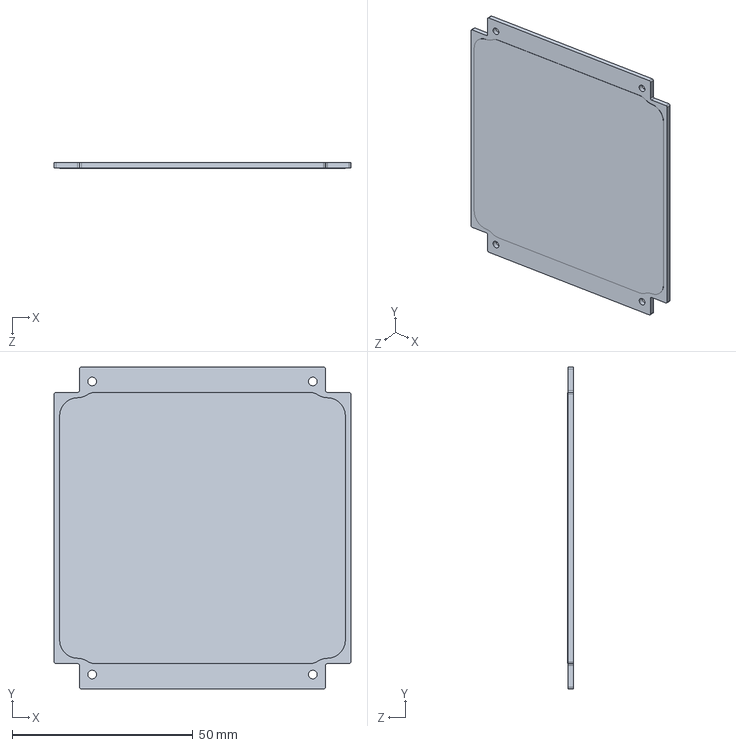
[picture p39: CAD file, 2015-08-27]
Materiais/Mecânica/CubeSat/Cubesat-PCB-Side-Eureka.SLDPRT
82.0 x 89.0 x 1.70 mm

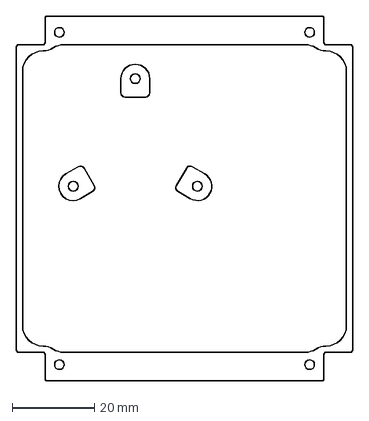
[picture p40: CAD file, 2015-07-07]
Materiais/Mecânica/Fabricação/PCB/Cubesat-PCB-Side-Ctrl-1.dxf
82.0 x 89.0 mm

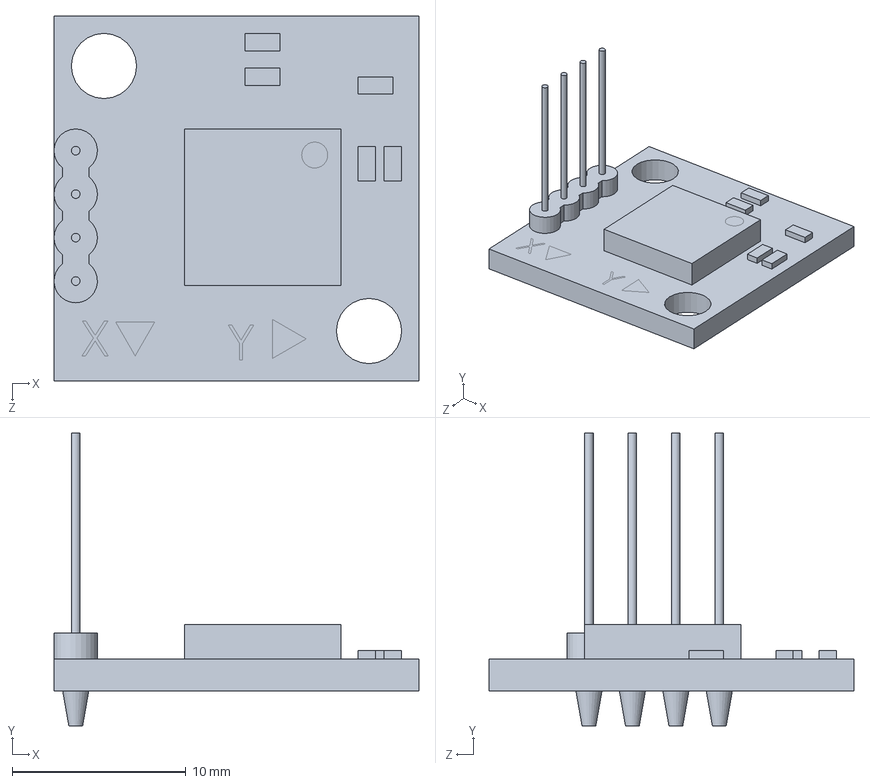
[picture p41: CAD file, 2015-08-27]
Materiais/Mecânica/Controle/IMU.SLDPRT
21.0 x 16.9 x 21.0 mm

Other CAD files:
Materiais/Mecânica/Controle/CubeSat Control.SLDASM
Materiais/Mecânica/Fabricação/CubeSat/DWG/Cubesat-Struct-Int-Plate-PCBStructHalf.DWG
Materiais/Mecânica/Fabricação/CubeSat/DWG/Cubesat-Struct-Int-Frame-Top.DWG
Materiais/Mecânica/CubeSat/Cubesat-PCB-Side-Ctrl-1.SLDPRT
Materiais/Mecânica/Base de Teste/51100.SLDPRT
Materiais/Mecânica/Base de Teste/Barra Roscada M6.SLDPRT
Materiais/Mecânica/Base de Teste/Base - Top.SLDPRT
Materiais/Mecânica/Base de Teste/Eixo.SLDPRT
Materiais/Mecânica/Base de Teste/Encoder.SLDPRT
Materiais/Mecânica/Base de Teste/Polar Graph.SLDPRT
Materiais/Mecânica/Base de Teste/Suporte Encoder.SLDPRT
Materiais/Mecânica/Controle/351100.SLDPRT
Materiais/Mecânica/Controle/Bluetooth.SLDPRT
Materiais/Mecânica/Controle/Roda Reação.SLDPRT
Materiais/Mecânica/Controle/Suporte Bateria.SLDPRT
Materiais/Mecânica/Controle/Suporte IMU.sldprt
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

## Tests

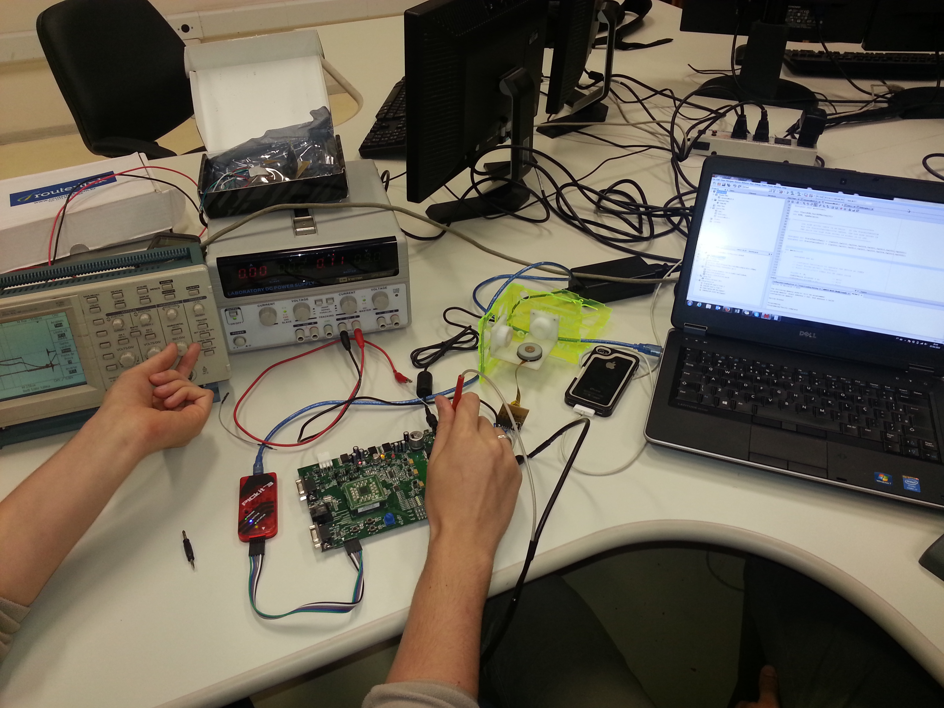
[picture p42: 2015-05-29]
Como/Artigos/Monografia/figs/Motor_Test.jpg

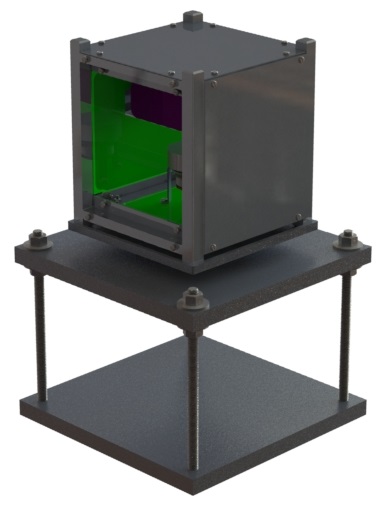
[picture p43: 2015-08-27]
Como/Artigos/Referências/Imagens/Base_Test_Cube.JPG

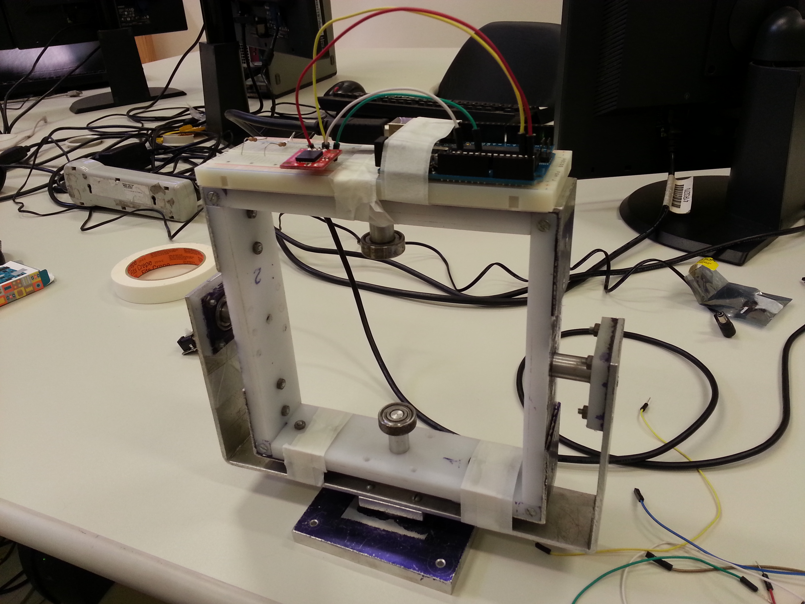
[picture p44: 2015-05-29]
Como/Artigos/Referências/Imagens/Teste com sensor - 2.jpg

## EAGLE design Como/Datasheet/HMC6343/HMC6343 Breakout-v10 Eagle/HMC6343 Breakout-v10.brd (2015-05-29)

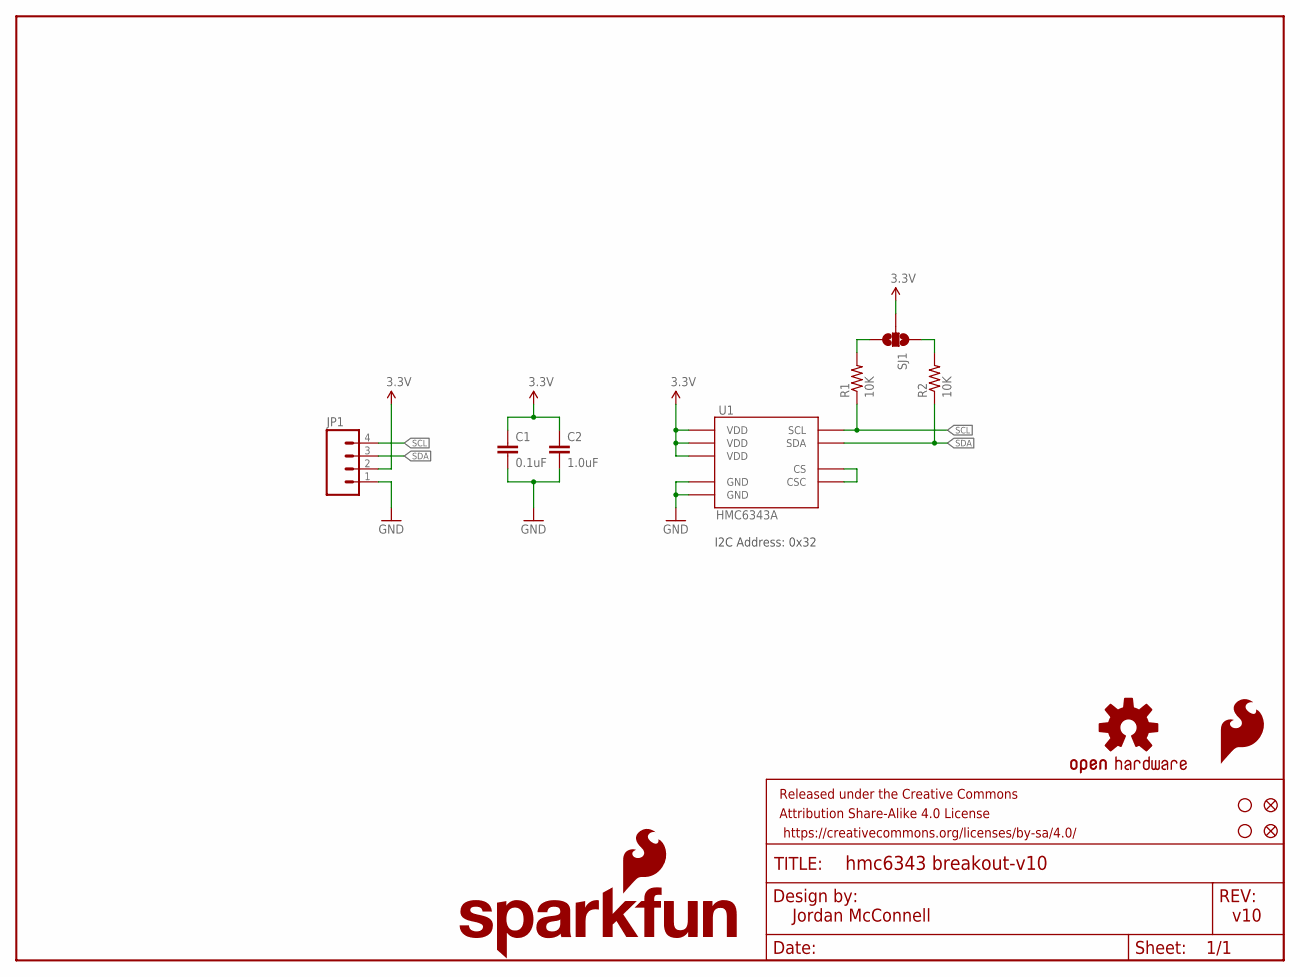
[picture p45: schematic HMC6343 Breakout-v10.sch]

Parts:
C1: 0.1uF; 0603-CAP
C2: 1.0uF; 0603-CAP
FID1, FID2: FIDUCIAL1X2; FIDUCIAL-1X2
FRAME1: FRAME-LETTER; CREATIVE_COMMONS
JP1: M04PTH; 1X04
LOGO1: SFE_LOGO_FLAME.1_INCH; SFE_LOGO_FLAME_.1
LOGO2: SFE_LOGO_NAME_FLAME.1_INCH; SFE_LOGO_NAME_FLAME_.1
LOGO3: OSHW-LOGOS; OSHW-LOGO-S
R1, R2: 10K; 0603-RES
SJ1: SOLDERJUMPER_2WAYPASTE1&2&3; SJ_3_PASTE1&2&3
STANDOFF1, STANDOFF2: STAND-OFF
U1: HMC6343A; LCC36

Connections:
3.3V: C1.1, C2.1, JP1.2, SJ1.2, U1.3 (VDD), U1.11 (VDD), U1.21 (VDD)
GND: C1.2, C2.2, JP1.1, U1.25 (GND), U1.29 (GND)
unnamed: U1.22 (CS), U1.35 (CSC)
unnamed: R1.2, SJ1.3
unnamed: R2.2, SJ1.1
SCL: JP1.4, R1.1, U1.32 (SCL)
SDA: JP1.3, R2.1, U1.36 (SDA)

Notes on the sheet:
Jordan McConnell
v10
I2C Address: 0x32

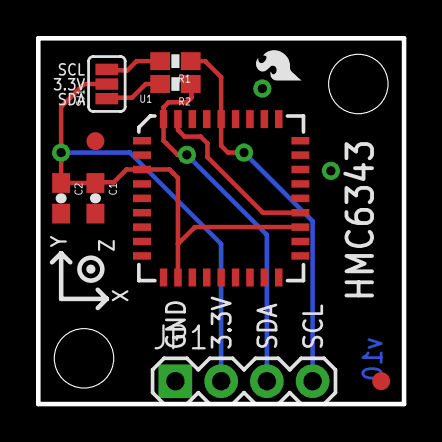
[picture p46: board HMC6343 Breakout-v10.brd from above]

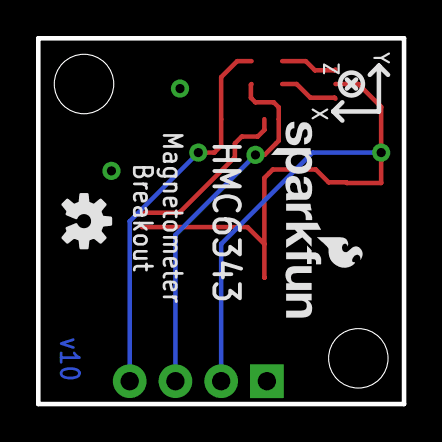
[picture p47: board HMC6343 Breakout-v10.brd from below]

Board: 2 copper layers, 20.3 x 20.3 mm, 15 parts (2 on the bottom side), 7 nets.

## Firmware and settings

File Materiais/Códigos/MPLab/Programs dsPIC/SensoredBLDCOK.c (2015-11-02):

//---------------------------------------------------------------------
//
//							 Software License Agreement
//
// The software supplied herewith by Microchip Technology Incorporated 
// (the “Company”) for its PICmicro® Microcontroller is intended and 
// supplied to you, the Company’s customer, for use solely and 
// exclusively on Microchip PICmicro Microcontroller products. The 
// software is owned by the Company and/or its supplier, and is 
// protected under applicable copyright laws. All rights are reserved. 
//  Any use in violation of the foregoing restrictions may subject the 
// user to criminal sanctions under applicable laws, as well as to 
// civil liability for the breach of the terms and conditions of this 
// license.
//
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
//---------------------------------------------------------------------
//	File:		SensoredBLDC.c
//
//	Written By:		Bill Anderson, Microchip Technology
//						
// 
// The following files should be included in the MPLAB project:
//
//		SensoredBLDC.c		-- Main source code file
//		Interrupts.c
//		Init.c
//		SensoredBLDC.h		-- Header file
//		p33FJ256MC710.gld	-- Linker script file
//				
//
//--------------------------------------------------------------------
//
// Revision History
//
// 06/30/07 -- first version 
//---------------------------------------------------------------------- 

#include "p33EP32MC202.h"
#include "SensoredBLDC.h"
#include "motorcontrol.h"

#include "pps.h"
#include<uart.h>
/******************************************************************************/
/* Configuration bits                                                         */
/******************************************************************************/

// Select Internal FRC at POR
_FOSCSEL(FNOSC_FRC & PWMLOCK_OFF & IESO_OFF);
// Enable Clock Switching and Configure POSC in XT mode

_FOSC(FCKSM_CSECMD & OSCIOFNC_OFF & POSCMD_XT);

_FPOR( ALTI2C1_ON & ALTI2C2_ON );
// ALTI2C1_ON           I2C1 mapped to ASDA1/ASCL1 pins
// ALTI2C2_ON           I2C2 mapped to ASDA2/ASCL2 pins

_FWDT(FWDTEN_OFF)

void InitOUT_5(void);
void InitStatusLED(void);
void InitADC0(void);
void DelayNmSec(unsigned int N);
void InitMCPWM(void);
void InitTMR3(void);
void InitIC(void);
void InitTMR1(void);
void motorcontrol (int state);

struct MotorFlags Flags;

int setpoint;
int velocidade;
unsigned int HallValue;
unsigned int timer3value;
unsigned int timer3avg;
unsigned int polecount = 0;
unsigned int dado, dado1, ADCValue;
unsigned int maquinaestados = 0;
unsigned int controleteste = 0;
 
char *UartRPM,UartRPMarray[5];
int RPM, rpmBalance,i;



/*************************************************************
 A tablea de acionamento segue a seguinte ordem:
 * Acionamento proporcionado através do DRV8313

State	OUTPUT1	OUTPUT2	OUTPUT3	HALLA	HALLB	HALLC	# Hall	Direto	Reverso
6	Float	High	Low	0	1	0	2	1	4
1	High	Float	Low	1	1	0	6	2	5
2	High	Low	Float	1	0	0	4	3	6
3	Float	Low	High	1	0	1	5	4	1
4	Low	Float	High	0	0	1	1	5	2
5	Low	High	Float	0	1	1	3	6	3
*
*************************************************************/

unsigned int StateTableFwd[] = {0, 5, 1, 6, 3, 4, 2, 0};
unsigned int StateTableRev[] = {0, 2, 4, 3, 6, 1, 5, 0};

int main(void)
{
	unsigned int i;

        // Configure PLL prescaler, PLL postscaler, PLL divisor
        PLLFBD=46; // M=48
        CLKDIVbits.PLLPOST=0; // N2=2
        CLKDIVbits.PLLPRE=0; // N1=2
        // Initiate Clock Switch to Primary Oscillator with PLL (NOSC=0b011)
        __builtin_write_OSCCONH(0x03);
        __builtin_write_OSCCONL(OSCCON | 0x01);
        // Wait for Clock switch to occur
        while (OSCCONbits.COSC!= 0b011);
        //  Wait for PLL to lock
        while (OSCCONbits.LOCK!= 1);

        TRISB=0b0000000000000000;		 	  	 //Configura o PORTB;
	TRISA=0b0000000000000000;		 	  	 //Configura o PORTA;

	// Analog pin for POT already initialized in ADC init subroutine

        /*Função para iniciar os imput captures para os sensores hall do motor
        *
        *RPI32 - RB0 - IC1 --> Hall 1
        *RPI33 - RB1 - IC2 --> Hall 2
        *RP39 - RB7 - IC3  --> Hall 3*/

        PPSInput(IN_FN_PPS_IC1, IN_PIN_PPS_RPI32); // Maps IC1 input to RPI32 pin
        PPSInput(IN_FN_PPS_IC2, IN_PIN_PPS_RPI33); // Maps IC2 input to RPI33 pin
        PPSInput(IN_FN_PPS_IC3, IN_PIN_PPS_RP39); // Maps IC3 input to R39 pin

	InitADC0();
	InitTMR1();
	InitTMR3();
	timer3avg = 0;
	InitMCPWM();
        Flags.RunMotor = 1;
	InitIC();
        InitStatusLED();
        InitOUT_5();

        for(i = 0;i<256;i++)
	{
		RAMBuffer[i] = i;	//Initlize RAMBuffer with some value
							//in case MasterI2C device wants to read
							//before it writes to it.
	}

        I2C1_PICs();
	Flags.Direction = 1;				// initialize direction CW
        RESET8313N = 0;
        SLEEP8313N = 0;
        MDC = 300; //Valores variam de PTPER a 0; - 0 = 100%
        

        while(1)
	{
         maquinaestados = RAMBuffer[0];
         if (FAULT8313N)
         {
           maquinaestados = 0;  
         }
         maquinaestados = 3;

            switch (maquinaestados)
            {
            case 0://Estado 0 --> Modo Falha/Desligado
                SLEEP8313N = 0;
                RESET8313N = 0;
                LED = 1;
            break;
            case 1://Estado 1 --> Modo Modo automático
                SLEEP8313N = 1;
                RESET8313N = 1;
                LED = 0;
                //calculasetpoint(RAMBuffer[20]);
                setpoint = 2000;
            break;
            case 2://Estado 1 --> Modo Modo Manual
                SLEEP8313N = 1;
                RESET8313N = 1;
                Flags.Direction = RAMBuffer[15];
                MDC = RAMBuffer[16]<<8+RAMBuffer[17];
            break;
            case 3:
                SLEEP8313N = 1;
                RESET8313N = 1;
                LED = 1;
                for (i=0;i<=10;i++)
                    {
                    DelayNmSec(10000); //Delay de 10s
                    }
                if (LED == 1)
                LED = 0;
                else
                LED = 1;
                switch(controleteste)
                {
                    case 0:
                setpoint = 0;
                controleteste = 2;
                    break;
                    case 1:
                setpoint = 2000;
                controleteste = 2;
                    break;
                    case 2:
                setpoint = 6000;
                controleteste = 3;
                    break;
                    case 3:
                setpoint = 2000;
                controleteste = 4;
                    break;
                case 4:
                setpoint = 0;
                controleteste = 5;
                    break;
                    case 5:
                setpoint = -2000;
                controleteste = 6;
                    break;
                    case 6:
                setpoint = -6000;
                controleteste = 7;
                    break;
                    case 7:
                setpoint = -2000;
                controleteste = 8;
                    break;
                    case 8:
                setpoint = 0;
                controleteste = 1;
                    break;
                }
            break; 
            }    
            
           
            //Atualiza Endereços de memória
            RAMBuffer[10] = PLED;
            RAMBuffer[11] = PRESET8313N;
            RAMBuffer[12] = PSLEEP8313N;
            RAMBuffer[13] = FAULT8313N;
            RAMBuffer[14] = Flags.RunMotor;
            RAMBuffer[15] = Flags.Direction;
            RAMBuffer[18] = MDC>>8;
            RAMBuffer[19] = MDC&0x00FF;

        //DelayNmSec(100);                 // Sample for 100 us
        //AD1CON1bits.SAMP = 0;         // Start the conversion
        //while (!AD1CON1bits.DONE);    // Wait for the conversion to complete
        ///AD1CON1bits.DONE = 0;         // Clear conversion done status bit
        //ADCValue = ADC1BUF0;          // Read the ADC conversion result

        //RAMBuffer[10] = ADCValue>>8;;
        //RAMBuffer[11] = ADCValue&0x00FF;

        

        //RAMBuffer[32] = timer3avg*60*234575;

		/*while(S2)					// wait for start key hit
		{
			if (!S3)				// check for direction change
			{
				while (!S3)			// wait till key is released
					DelayNmSec(10);
					Flags.Direction ^= 1;
			}
			Nop();
		}
		while (!S2)					// wait till key is released
		DelayNmSec(10);
			
			// read hall position sensors on PORTD
		HallValue = (unsigned int)((PORTB >> 1) & 0x0007);
		//if (Flags.Direction)
			//OVDCON = StateTableFwd[HallValue];
		//else
			//OVDCON = StateTableRev[HallValue];
			
		PWMCON1 = 0x0777;			// enable PWM outputs
		Flags.RunMotor = 1;			// set flag
		T3CONbits.TON = 1;			// start tmr3
		polecount = 1;
		DelayNmSec(100);

		while (Flags.RunMotor)				// while motor is running
		{
			if (!S2)						// if S2 is pressed
				{
				PWMCON1 = 0x0700;			// disable PWM outputs
  				//OVDCON = 0x0000;			// overide PWM low.
				Flags.RunMotor = 0;			// reset run flag
				while (!S2)					// wait for key release
					DelayNmSec(10);
				}
			Nop();
		}*/
	}
}
//---------------------------------------------------------------------
// This is a generic 1ms delay routine to give a 1mS to 65.5 Seconds delay
// For N = 1 the delay is 1 mS, for N = 65535 the delay is 65,535 mS. 
// Note that FCY is used in the computation.  Please make the necessary
// Changes(PLLx4 or PLLx8 etc) to compute the right FCY as in the define
// statement above.
void DelayNmSec(unsigned int N)
{
unsigned int j;
while(N--)
 	for(j=0;j < MILLISEC;j++);
}

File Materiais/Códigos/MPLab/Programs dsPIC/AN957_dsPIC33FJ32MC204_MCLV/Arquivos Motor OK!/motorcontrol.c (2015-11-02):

#include <stdio.h>
#include <stdlib.h>
#include "p33EP32MC202.h"
#include "SensoredBLDC.h"
#include "motorcontrol.h"

int state;

void motorcontrol (int state)
{
 switch(state){
        case 0:
        EN1 = 0;
        IOCON1bits.OVRENH = 1;  //Turn overide ON for high pin - PWM OFF
        IOCON1bits.OVRDAT1 = 1; // PWM High Pin override output is off = 0;
        EN2 =0;
        IOCON2bits.OVRENH = 1;  //Turn overide ON for high pin - PWM OFF
        IOCON2bits.OVRDAT1 = 1; // PWM High Pin override output is off = 0;
        EN3 =0;
        IOCON3bits.OVRENH = 1;  //Turn overide ON for high pin - PWM OFF
        IOCON3bits.OVRDAT1 = 1; // PWM High Pin override output is off = 0;
        break;
        case 1:
        EN1 = 0;
        IOCON1bits.OVRENH = 1;  //Turn overide ON for high pin - PWM OFF
        IOCON1bits.OVRDAT1 = 1; // PWM High Pin override output is off = 0;
        EN2 =1;
        IOCON2bits.OVRENH = 0;  //Turn overide off for high pin - PWM Enabled
        EN3 =1;
        IOCON3bits.OVRENH = 1;  //Turn overide ON for high pin - PWM OFF
        IOCON3bits.OVRDAT1 = 1; // PWM High Pin override output is off = 0;
        break;
        case 2:
        EN1 =1;
        IOCON1bits.OVRENH = 0;  //Turn overide off for high pin - PWM Enabled
        EN2 =0;
        IOCON2bits.OVRENH = 1;  //Turn overide ON for high pin - PWM OFF
        IOCON2bits.OVRDAT1 = 1; // PWM High Pin override output is off = 0;
        EN3 =1;
        IOCON3bits.OVRENH = 1;  //Turn overide ON for high pin - PWM OFF
        IOCON3bits.OVRDAT1 = 1; // PWM High Pin override output is off = 0;
        break;
        case 3:
        EN1 =1;
        IOCON1bits.OVRENH = 0;  //Turn overide off for high pin - PWM Enabled
        EN2 =1;
        IOCON2bits.OVRENH = 1;  //Turn overide ON for high pin - PWM OFF
        IOCON2bits.OVRDAT1 = 1; // PWM High Pin override output is off = 0;
        EN3 =0;
        IOCON3bits.OVRENH = 1;  //Turn overide ON for high pin - PWM OFF
        IOCON3bits.OVRDAT1 = 1; // PWM High Pin override output is off = 0;
        break;
        case 4:
        EN1 =0;
        IOCON1bits.OVRENH = 1;  //Turn overide ON for high pin - PWM OFF
        IOCON1bits.OVRDAT1 = 1; // PWM High Pin override output is off = 0;
        EN2 =1;
        IOCON2bits.OVRENH = 1;  //Turn overide ON for high pin - PWM OFF
        IOCON2bits.OVRDAT1 = 1; // PWM High Pin override output is off = 0;
        EN3 =1;
        IOCON3bits.OVRENH = 0;  //Turn overide off for high pin - PWM Enabled
        break;
        case 5:
        EN1 =1;
        IOCON1bits.OVRENH = 1;  //Turn overide ON for high pin - PWM OFF
        IOCON1bits.OVRDAT1 = 1; // PWM High Pin override output is off = 0;
        EN2 =0;
        IOCON2bits.OVRENH = 1;  //Turn overide ON for high pin - PWM OFF
        IOCON2bits.OVRDAT1 = 1; // PWM High Pin override output is off = 0;
        EN3 =1;
        IOCON3bits.OVRENH = 0;  //Turn overide off for high pin - PWM Enabled
        break;
        case 6:
        EN1 =1;
        IOCON1bits.OVRENH = 1;  //Turn overide ON for high pin - PWM OFF
        IOCON1bits.OVRDAT1 = 1; // PWM High Pin override output is off = 0;
        EN2 =1;
        IOCON2bits.OVRENH = 0;  //Turn overide off for high pin - PWM Enabled
        EN3 =0;
        IOCON3bits.OVRENH = 1;  //Turn overide ON for high pin - PWM OFF
        IOCON3bits.OVRDAT1 = 1; // PWM High Pin override output is off = 0;
        break;
        case 7:
        EN1 = 0;
        IOCON1bits.OVRENH = 1;  //Turn overide ON for high pin - PWM OFF
        IOCON1bits.OVRDAT1 = 1; // PWM High Pin override output is off = 0;
        EN2 =0;
        IOCON2bits.OVRENH = 1;  //Turn overide ON for high pin - PWM OFF
        IOCON2bits.OVRDAT1 = 1; // PWM High Pin override output is off = 0;
        EN3 =0;
        IOCON3bits.OVRENH = 1;  //Turn overide ON for high pin - PWM OFF
        IOCON3bits.OVRDAT1 = 1; // PWM High Pin override output is off = 0;
        break;
    }
}

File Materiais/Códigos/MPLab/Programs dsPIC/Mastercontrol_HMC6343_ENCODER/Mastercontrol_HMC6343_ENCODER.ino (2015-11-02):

/******************************************************************************
HMC6343_basics.ino
Simple example for using the HMC6343 3-axis compass library.
Jordan McConnell @ SparkFun Electronics
17 July 2014
https://github.com/sparkfun/HMC6343_Breakout
This example declares an SFE_HMC6343 object called compass. The object/sensor
is initialized and if the initialization fails, the sensor could not
be found and read from successfully.
Each time through the loop, heading values (heading, pitch, and roll) and
accelerometer values (accelX, accelY, accelZ) are read from the sensor. They
are then printed to the Serial Monitor at 115200 baud. The raw sensor values
are printed as well as scaled values in readable units (degrees and g forces).
The HMC6343 breakout board needs to be powered with 3.3V and uses I2C to talk
to the microcontroller. If you're using a 5V microcontroller board, such as
the standard Arduino UNO, you'll need a Logic Level Converter for the I2C lines,
such as SparkFun's BOB-12009.
Developed/Tested with:
Arduino Uno
Arduino IDE 1.0.5 & 1.5.2
Requires:
SFE_HMC6343_Library
This code is beerware.
Distributed as-is; no warranty is given.
******************************************************************************/
// Libraries for I2C and the HMC6343 sensor
#include <Wire.h>
#include "SFE_HMC6343.h"
SFE_HMC6343 compass; // Declare the sensor object

int setpointvelocidade = 0;
int setpoint = 30;
int setpointzero = 0;
float setpointnovareferencia = 0;
float setpointrad;//3.141592653589793;
float anguloatual;
char recebe;
float uk = 0;
float uk1 = 0;
float uk2 = 0;
float ek = 0;
float ek1 = 0;
float ek2 = 0;

int clk = 8;
int Data = 4;
int csn = 7;
char D11 = 0;
char D10 = 0;
char D9 = 0;
char D8 = 0;
char D7 = 0;
char D6 = 0;
char D5 = 0;
char D4 = 0;
char D3 = 0;
char D2 = 0;
char D1 = 0;
char D0 = 0;
int Resposta;
float Angulo;

void setup()
{
// Start serial communication at 115200 baud
Serial.begin(9600);
  pinMode(clk, OUTPUT);
  pinMode(Data, INPUT);
  pinMode(csn, OUTPUT);
  delay(100);
// Give the HMC6343 a half second to wake up
//delay(500);
// Initialize the HMC6343 and verify its physical presence
//  if (!compass.init())
//  {
//  Serial.println("Sensor Initialization Failed\n\r"); // Report failure, is the sensor wiring correct?
//  }

}
void loop()
{
// Read, calculate, and print the heading, pitch, and roll from the sensor
//compass.readHeading();
//printHeadingData();

///Mudança de variaveis para evitar singularidade

  //setpointnovareferencia = (compass.heading/10.0) - setpoint; IMU
  
  digitalWrite(clk,HIGH);
  digitalWrite(csn,HIGH);
  delayMicroseconds(1);

  digitalWrite(csn,LOW);
  delayMicroseconds(1);

  digitalWrite(clk,LOW);
  delayMicroseconds(1);
  digitalWrite(clk,HIGH);
  D11 = digitalRead(Data);
  delayMicroseconds(1);

  digitalWrite(clk,LOW);
  delayMicroseconds(1);
  digitalWrite(clk,HIGH);
  D10 = digitalRead(Data);
  delayMicroseconds(1);

  digitalWrite(clk,LOW);
  delayMicroseconds(1);
  digitalWrite(clk,HIGH);
  D9 = digitalRead(Data);
  delayMicroseconds(1);

  digitalWrite(clk,LOW);
  delayMicroseconds(1);
  digitalWrite(clk,HIGH);
  D8 = digitalRead(Data);
  delayMicroseconds(1);

  digitalWrite(clk,LOW);
  delayMicroseconds(1);
  digitalWrite(clk,HIGH);
  D7 = digitalRead(Data);
  delayMicroseconds(1);

  digitalWrite(clk,LOW);
  delayMicroseconds(1);
  digitalWrite(clk,HIGH);
  D6 = digitalRead(Data);
  delayMicroseconds(1);

  digitalWrite(clk,LOW);
  delayMicroseconds(1);
  digitalWrite(clk,HIGH);
  D5 = digitalRead(Data);
  delayMicroseconds(1);

  digitalWrite(clk,LOW);
  delayMicroseconds(1);
  digitalWrite(clk,HIGH);
  D4 = digitalRead(Data);
  delayMicroseconds(1);

  digitalWrite(clk,LOW);
  delayMicroseconds(1);
  digitalWrite(clk,HIGH);
  D3 = digitalRead(Data);
  delayMicroseconds(1);

  digitalWrite(clk,LOW);
  delayMicroseconds(1);
  digitalWrite(clk,HIGH);
  D2 = digitalRead(Data);
  delayMicroseconds(1);

  digitalWrite(clk,LOW);
  delayMicroseconds(1);
  digitalWrite(clk,HIGH);
  D1 = digitalRead(Data);
  delayMicroseconds(1);

  digitalWrite(clk,LOW);
  delayMicroseconds(1);
  digitalWrite(clk,HIGH);
  D0 = digitalRead(Data);
  delayMicroseconds(1);
  
  Resposta = 2048*D11 + 1024*D10 + 512*D9 + 256*D8 + 128*D7 + 64*D6 + 32*D5 + 16*D4 + 8*D3 + 4*D2 + 2*D1 + 1*D0;
  
  Angulo = 0.087890625*Resposta;
  Serial.println(Angulo);
  
  setpointnovareferencia = Angulo - setpoint; //ENCODER
  
  if (setpointnovareferencia >=180.0)
  {
   setpointnovareferencia = setpointnovareferencia-360;
  }

  Serial.println(setpointnovareferencia);
  
  anguloatual =  (((setpointnovareferencia)*3.141592653589793)/180);                                     //(((compass.heading/10.0)*3.141592653589793)/180);
  setpointrad = ((setpointzero*3.141592653589793)/180);                    //((setpoint*3.141592653589793)/180);
  
  ek = setpointrad - anguloatual; 

  //uk = uk1 + 189.95*ek - 169.2075*ek1; //PI do angelo

  uk = 150*ek;// Proporcional 
  
  //uk = 1.6498*uk1 - 0.6498*uk2 + 52.418*ek + 0.08911*ek1 - 52.051*ek2; //PID 
  
  // uk = uk1 + 0.023107314300773*ek - 0.022561042095081*ek1; //Equação de PI que não funciona ek muito baixo;
   
  //uk = 1.932*uk1 - 0.9316*uk2 + 127.5*ek - 254.6*ek1 + 127.1*ek2; //Uma nova esperaça
  
  //uk = -1.422*uk1 + 264.2*ek + 29.36*ek1 + 0.2367*ek2; //Uma nova esperaça 2
  
  
  //Serial.println(uk,3);
  //Serial.println(uk1,3);
  //Serial.println(uk2,3);
  Serial.println(ek,3);
  //Serial.println(ek1,3);
  //Serial.println(ek2,3);
  //Serial.println();
  
  setpointvelocidade = -1*((uk*30)/3.141592653589793); //Mudar o sentido de rotação do conjunto.
  
  Serial.println(setpointvelocidade);
  Serial.println();

//  enviaI2C(64,20,((setpointvelocidade>>8)));
//  enviaI2C(64,21,(setpointvelocidade&0x00FF));     
//  enviaI2C(64,0,1); 
//  //enviaI2C(64,20,-7);
//  //enviaI2C(64,21,208);     
//  //recebe = recebeI2C(64,0);
//  //Serial.println(recebe);
//  //Serial.println();
//  
//    
  uk2 = uk1;
  ek2 = ek1;
  uk1 = uk;
  ek1 = ek;

delay(1000); // Minimum delay of 200ms (HMC6343 has 5Hz sensor reads/calculations)
}
// Print both the raw values of the compass heading, pitch, and roll
// as well as calculate and print the compass values in degrees
// Sample Output:
// Heading Data (Raw value, in degrees):
// Heading: 3249 324.90°
void printHeadingData()
{
Serial.println("Heading Data (Raw value, in degrees):");
Serial.print("Heading: ");
//Serial.print(compass.heading); Serial.print(" "); // Print raw heading value
Serial.print((float) compass.heading/10.0);/*Serial.write(176)*/;Serial.println(); // Print heading in degrees
}

void enviaI2C(byte who, byte adress, byte data)
{
Wire.beginTransmission(who);
Wire.write(adress);        
Wire.write(data);        
Wire.endTransmission();   
}
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

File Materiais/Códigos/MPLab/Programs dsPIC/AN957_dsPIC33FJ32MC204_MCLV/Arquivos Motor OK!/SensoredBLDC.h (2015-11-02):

//---------------------------------------------------------------------
//
//							 Software License Agreement
//
// The software supplied herewith by Microchip Technology Incorporated 
// (the “Company”) for its PICmicro® Microcontroller is intended and 
// supplied to you, the Company’s customer, for use solely and 
// exclusively on Microchip PICmicro Microcontroller products. The 
// software is owned by the Company and/or its supplier, and is 
// protected under applicable copyright laws. All rights are reserved. 
//  Any use in violation of the foregoing restrictions may subject the 
// user to criminal sanctions under applicable laws, as well as to 
// civil liability for the breach of the terms and conditions of this 
// license.
//
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
//---------------------------------------------------------------------
//	File:		SensoredBLDC.h
//
//						
// 
// The following files should be included in the MPLAB project:
//
//		SensoredBLDC.c		-- Main source code file
//		Interrupts.c
//		Init.c
//		SensoredBLDC.h		-- Header file
//		p33FJ32MC204.gld	-- Linker script file
//				
//
//---------------------------------------------------------------------- 

/*
Using the Fosc = Fin * (M/(N1*N2))
Where:
Fin 	= 8Mhz
M 	= PLLFBD[PLLDIV<8:0>] 	= 0x26	then M = 40  (PLLDIV + 2)
N1	= CLKDIV[PLLPRE<4:0>] 	= 0x0 	then N1 = 2  (PLLPRE + 2)
N2	= CLKDIV[PLLPOST<1:0>]	= 0x3	then N2 = 8 

CLKDIV = 0x30C0
PLLFBD = 0x0026

?	Fosc =	(8M * (40 / (8 * 2)))  = 20Mhz
?	Fcy  =	20M/2 = 10MIP
*/

//#define CLOSEDLOOP
#define FOSC  120000000			// xtal = 10.0Mhz, 120.0Mhz after PLL
#define FCY  FOSC/2				
#define MILLISEC FCY/60000		// 1 mSec delay constant
#define FPWM 39000

#define POLEPAIRS		4		// number of pole pairs
#define HALL_INDEX_R	6		// Hall sensor position index
#define HALL_INDEX_F	5		// Hall sensor position index

#define LED     LATAbits.LATA1
#define	PLED	PORTAbits.RA1
#define EN1     LATBbits.LATB15
#define EN2     LATBbits.LATB13
#define EN3     LATBbits.LATB11
#define RESET8313N LATAbits.LATA4
#define SLEEP8313N LATBbits.LATB5
#define FAULT8313N PORTBbits.RB6
#define PRESET8313N PORTAbits.RA4
#define PSLEEP8313N PORTBbits.RB5
#define HALL1	PORTBbits.RB0
#define HALL2	PORTBbits.RB1
#define HALL3	PORTBbits.RB7

#define T1PR1 ((FCY/1000)/8)

/* Based on using the internal Fcy and Timer 3 prescaler of 256
 * Fcy/256 = 10M/256 = 39062.5 ticks/sec
 * or, 2343750 ticks = 1RPM
 * => RPM would be 2343750/T3ticks
 */
//#define SPEEDMULT	2343750
//define OFFSET 8
//#define POTMULT 4				// pot to speed ratio

//#define Kps	50					// Kp and Ks terms need to be adjusted
//#define Kis	1					// as per the motor and load 

struct MotorFlags
{
unsigned RunMotor 	:1;
unsigned Direction	:1;
unsigned Sentido	:1;
unsigned unused		:13;
};
extern struct MotorFlags Flags;

extern int setpoint;
extern int velocidade;
extern int velocidade1;
extern unsigned int HallValue;
extern unsigned int timer3value;
extern unsigned int timer3avg;
extern unsigned int timer1value;
extern unsigned int timer1avg;
extern unsigned int polecount;

extern unsigned int StateTableFwd[];
extern unsigned int StateTableRev[];

extern unsigned char RAMBuffer[256];	//RAM area which will work as EEPROM for Master I2C device

struct FlagType
{
	unsigned char AddrFlag:1;
	unsigned char DataFlag:1;
};
extern struct FlagType Flag;

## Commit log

2015-05-06 versao nova da placa de acionamento com outro ampop
    [Shield.brd, Shield.sch]
2015-05-07 adicionado BOM e PCB lucas
    [Shield.brd, Shield.sch, componente_pcb_bldc.xlsx]
2015-05-28 V1
    Primeiro upload das placas de controle dos motores
    [Circuito.sch]
2015-05-28 Revert "V1"
    This reverts commit c67eeae46dcaf9f8b5f9b61616df49a076ec1c0c.
    [Circuito.sch]
2015-05-29 Remoção de pasta de exemplo
    [Shield.brd, Shield.sch, componente_pcb_bldc.xlsx]
2015-05-29 Correção do local onde fica o Datasheet
    [HMC6343 Breakout-v10.brd, HMC6343 Breakout-v10.sch]
2015-05-29 Correção de onde ficam os arquivos de materiais
2015-05-31 Modelo Solid
    [CubeSat-Toolbox-Int-Nut-M1.6.SLDPRT, CubeSat-Toolbox-Int-PlateStruct.SLDPRT, CubeSat-Toolbox-Int-Screw-M1.6-12mm.SLDPRT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]
2015-05-31 Modelo do Motor
2015-06-02 Imagem Roda de Reação
2015-06-04 Folhas de fabricação
2015-06-06 Correção do modelo usado
    [CubeSat-Toolbox-Int-Nut-M1.6.SLDPRT, CubeSat-Toolbox-Int-PlateStruct.SLDPRT, CubeSat-Toolbox-Int-Screw-M1.6-12mm.SLDPRT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]
2015-06-07 CubeSat Control
    [351100.SLDPRT, Bateria.SLDPRT, Conjunto Motor.SLDASM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]
2015-06-08 Placas PCB
    Atualização das placas PCB no SolidWorks para futura conversão para o
    Eagle
    [Bluetooth.SLDPRT, CubeSat Control.SLDASM, CubeSat Eureka.SLDASM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]
2015-07-01 Orçamentos
    [Form direct sell-Treffer-IMT.xlsx]
2015-07-06 Atualizações mecânicas
    [Conjunto IMU.SLDASM, Conjunto Motor.SLDASM, CubeSat Control.SLDASM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]
2015-07-07 Modelo em SolidWorks
    [Conjunto Motor.SLDASM, CubeSat Control.SLDASM, CubeSat Eureka.SLDASM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]
2015-07-13 Arquivos para Impressão 3D
    [Suporte_Motor_E2.STL, Suporte_Motor_L.STL, Suporte_Motor_T.STL]
2015-07-15 Atualização Fabricação
    [Conjunto Motor.SLDASM, CubeSat Control.SLDASM, Cubesat-PCB-Side-Ctrl-1.SLDPRT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]
2015-08-06 Atualização SolidWorks
    [51100.SLDPRT, Barra Roscada M6.SLDPRT, Base - Low.SLDPRT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]
2015-08-15 Atualização Modelos SolidWorks
    [Base - Top.SLDPRT, Base de Teste.SLDASM, Cubesat-Struct-Ext-Shell-Side-1U.DWG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]
2015-08-27 Atualização Imagens de Referências
2015-08-27 Atualização Materiais
    [Lista de Componentes.xlsx, Lista de Materiais Mecânicos.xlsx]
2015-08-27 Remoção Imagens de Materiais
2015-11-02 Atualizações Gerais P3
    [Endereços de Memória.xlsx, PTPER.xlsx, comutate.xlsx]
2015-11-02 Atualizações Gerais P4
    [Tabela de conversão de layout DRV8811 para DRV8313.xlsx, botpanico v1.2.PrjPcb, botpanico v1.SchDoc]

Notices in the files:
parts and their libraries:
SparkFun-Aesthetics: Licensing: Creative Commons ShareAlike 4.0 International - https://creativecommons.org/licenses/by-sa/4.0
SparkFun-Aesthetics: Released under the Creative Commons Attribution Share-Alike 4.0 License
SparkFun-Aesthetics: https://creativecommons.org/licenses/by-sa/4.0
